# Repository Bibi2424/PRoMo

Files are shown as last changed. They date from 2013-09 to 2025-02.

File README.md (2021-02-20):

# PRoMo

## "Plateforme pour la Robotique Mobile"

### Mobile Robotic Plateform

This project is about creating a mobile robot from scratch.
There are four major parts in this project :

- Mechanics : Build a differential drive plateform with two DC motors with encoders. The different components must be build with Laser cutting and 3D printing (from low cost websites).
			
- Electronics : Create a main board based on a STM32F4 microcontroller with many components like motors, sensors, actuators, RF transmitters...
			
- Firmware : This can go two ways:
	- Provide a sets of high level librairies for controlling a sets of sensors and actuators and example projects, 
	- Give the code as is but with a performant way of interfacing with it (serial communication)

- Documentation : All the informations to understand the project will be there, with some tutorials. At the moment, used to store local datasheets
			
The aim of this projects is to propose some basics to start mobile robotic for the beginners and to simplify things for advanced people.

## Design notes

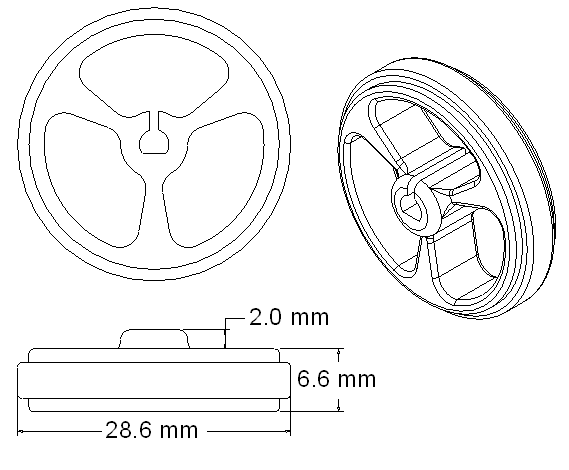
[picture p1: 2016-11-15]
Mechanics/Documentation/Wheel Pololu 32x7.png

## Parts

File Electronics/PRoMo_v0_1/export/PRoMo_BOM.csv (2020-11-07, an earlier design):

Comment | Designator | Footprint | LCSC
100nF | C1,C4,C5,C7,C9,C10,C13,C27,C28,C37,C39 | Capacitor_SMD:C_0805_2012Metric_Pad1.15x1.40mm_HandSolder | C49678
10uF | C11,C32 | Capacitor_SMD:C_0805_2012Metric_Pad1.15x1.40mm_HandSolder | C15850
1uF | C12 | Capacitor_SMD:C_0805_2012Metric_Pad1.15x1.40mm_HandSolder | C28323
4.7uF | C40 | Capacitor_SMD:C_0805_2012Metric_Pad1.15x1.40mm_HandSolder | C1779
18pF | C2,C3 | Capacitor_SMD:C_0805_2012Metric_Pad1.15x1.40mm_HandSolder | C1797
10nF | C26,C30 | Capacitor_SMD:C_0805_2012Metric_Pad1.15x1.40mm_HandSolder | C1710
2.2nF | C29 | Capacitor_SMD:C_0805_2012Metric_Pad1.15x1.40mm_HandSolder | C28260
2.2uF | C6,C8,C31 | Capacitor_SMD:C_0805_2012Metric_Pad1.15x1.40mm_HandSolder | C49217
10uF | C35 | Capacitor_Tantalum_SMD:CP_EIA-3216-18_Kemet-A_Pad1.58x1.35mm_HandSolder | C7171
SS14 | D14 | Diode_SMD:D_SMA_Handsoldering | C2480
LED_Red | D15 | LED_SMD:LED_0805_2012Metric_Pad1.15x1.40mm_HandSolder | C84256
LED_Yellow | D16 | LED_SMD:LED_0805_2012Metric_Pad1.15x1.40mm_HandSolder | C2296
LED_Green | D17,D18 | LED_SMD:LED_0805_2012Metric_Pad1.15x1.40mm_HandSolder | C2297
D_Zener_Small | D19 | Diode_SMD:D_SMA_Handsoldering | C2480
LED_Blue | D1,D2 | LED_SMD:LED_0805_2012Metric_Pad1.15x1.40mm_HandSolder | C2293
Yellow | D20,D21 | LED_SMD:LED_0805_2012Metric_Pad1.15x1.40mm_HandSolder | C2296
22uh | L1 | Inductor_SMD:L_0805_2012Metric_Pad1.15x1.40mm_HandSolder | C32375
10k | R11,R14 | Resistor_SMD:R_0805_2012Metric_Pad1.15x1.40mm_HandSolder | C17414
47R | R12,R13,R24 | Resistor_SMD:R_0805_2012Metric_Pad1.15x1.40mm_HandSolder | C17714
47k | R20 | Resistor_SMD:R_0805_2012Metric_Pad1.15x1.40mm_HandSolder | C17713
470R | R21 | Resistor_SMD:R_0805_2012Metric_Pad1.15x1.40mm_HandSolder | C17710
330R | R22 | Resistor_SMD:R_0805_2012Metric_Pad1.15x1.40mm_HandSolder | C17630
220R | R23,R25,R26 | Resistor_SMD:R_0805_2012Metric_Pad1.15x1.40mm_HandSolder | C17557
STM32F405RGTx | U1 | Package_QFP:LQFP-64_10x10mm_P0.5mm | C15742
FT232RL | U11 | Package_SO:SSOP-28_5.3x10.2mm_P0.65mm | C8690
MPU-6050 | U6 | Sensor_Motion:InvenSense_QFN-24_4x4mm_P0.5mm | C24112
DRV8833PWP | U7 | Package_SO:HTSSOP-16-1EP_4.4x5mm_P0.65mm_EP3.4x5mm_Mask2.46x2.31mm_ThermalVias | C50506
LM2596S-5 | U8 | Package_TO_SOT_SMD:TO-263-5_TabPin3 | C10002
AMS1117-3.3 | U9 | Package_TO_SOT_SMD:SOT-223-3_TabPin2 | C6186
Crystal 25MHz | Y1 | Crystal:Crystal_SMD_3225-4Pin_3.2x2.5mm_HandSoldering | C9006

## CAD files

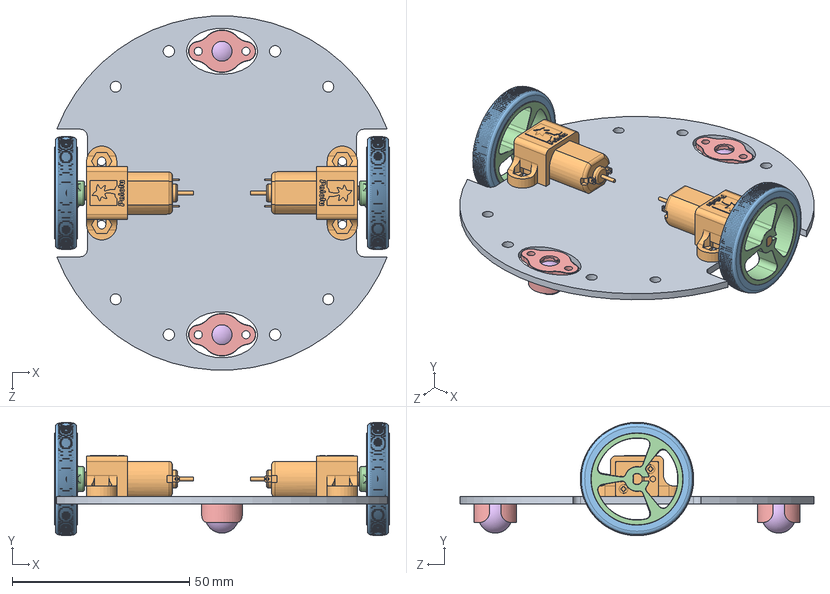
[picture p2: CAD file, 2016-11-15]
Mechanics/PRoMo_v0.1.SLDASM
94.5 x 32.0 x 99.8 mm
Support_bottom
micro-metal-gearmotor-extended-with-1086-bracket x 2
Pololu-Wheel-32x7mm-tire x 2
Pololu-Wheel-32x7mm-rim x 2
Caster x 2
Ball x 2

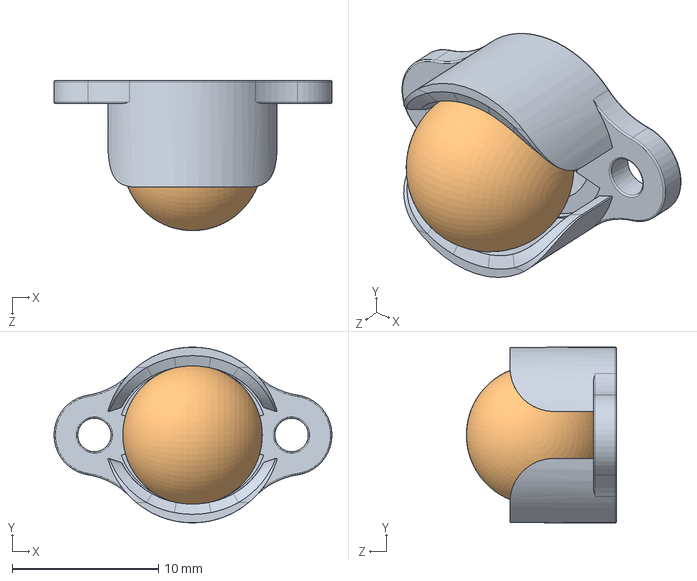
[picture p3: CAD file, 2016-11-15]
Mechanics/Pololu Ball Caster with 3_8_ Metal Ball.SLDASM
19.0 x 12.0 x 10.3 mm
Caster
Ball

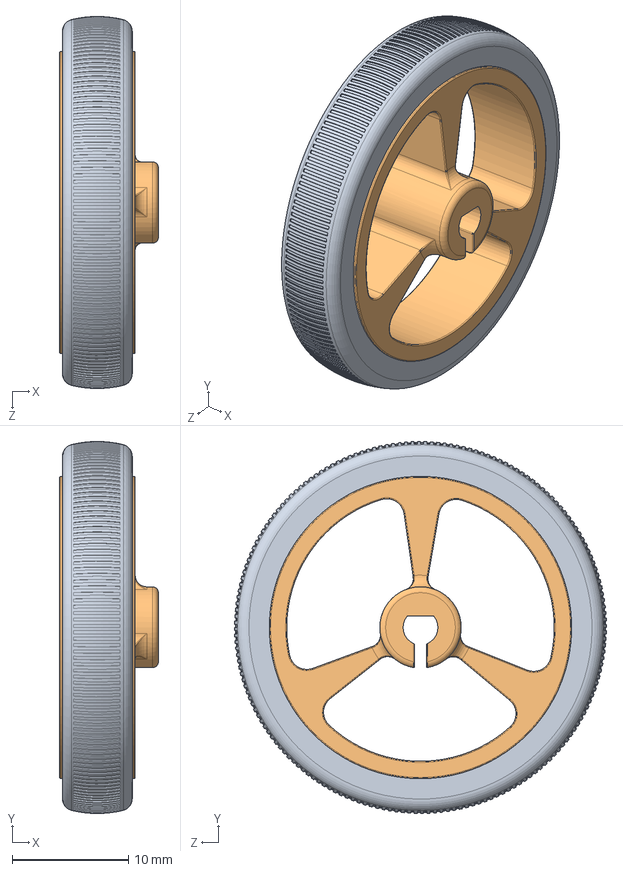
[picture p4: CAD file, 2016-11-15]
Mechanics/Pololu-Wheel-32x7mm.SLDASM
8.50 x 32.0 x 32.0 mm
Pololu-Wheel-32x7mm-tire
Pololu-Wheel-32x7mm-rim

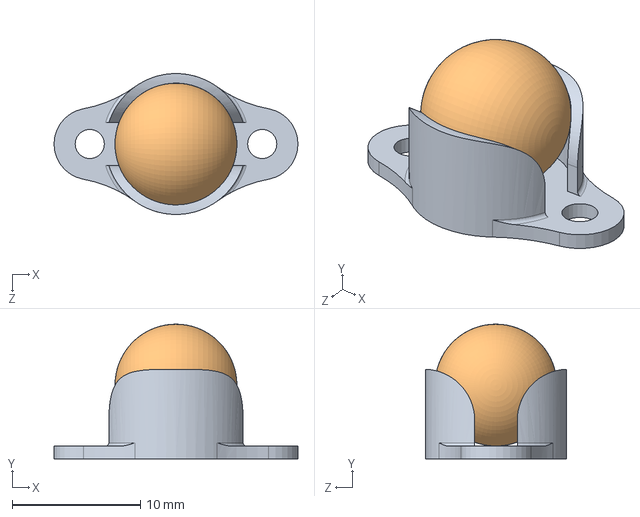
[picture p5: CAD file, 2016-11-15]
Mechanics/Caster ball assembly.SLDASM
19.1 x 10.5 x 11.0 mm
caster ball frame
caster ball

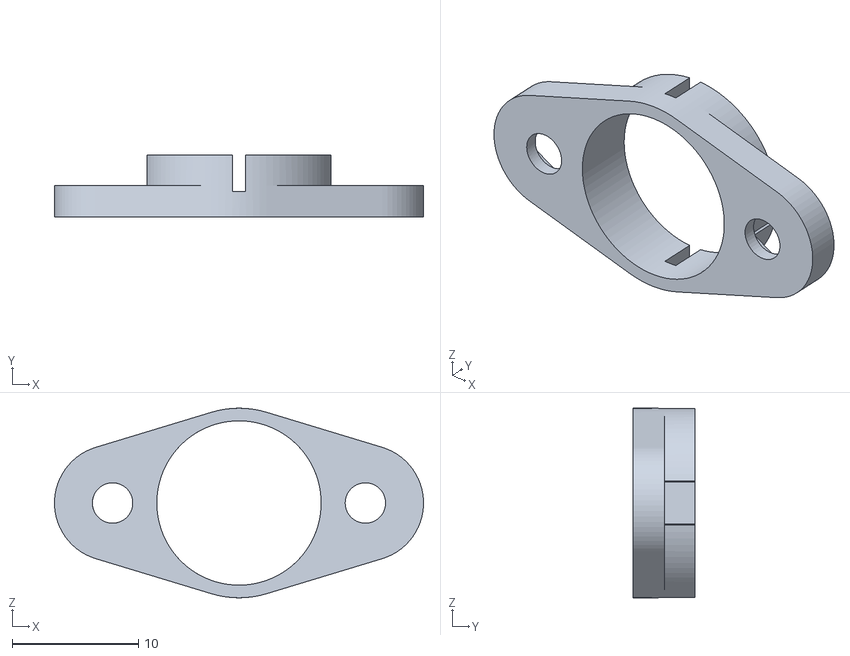
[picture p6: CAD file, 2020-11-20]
Mechanics/BallCaster Support.stl
29.2 x 4.90 x 15.0

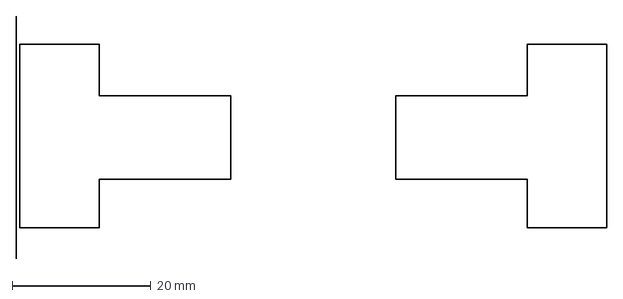
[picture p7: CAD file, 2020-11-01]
Mechanics/Motor_outline.dxf
85.2 x 35.0 mm

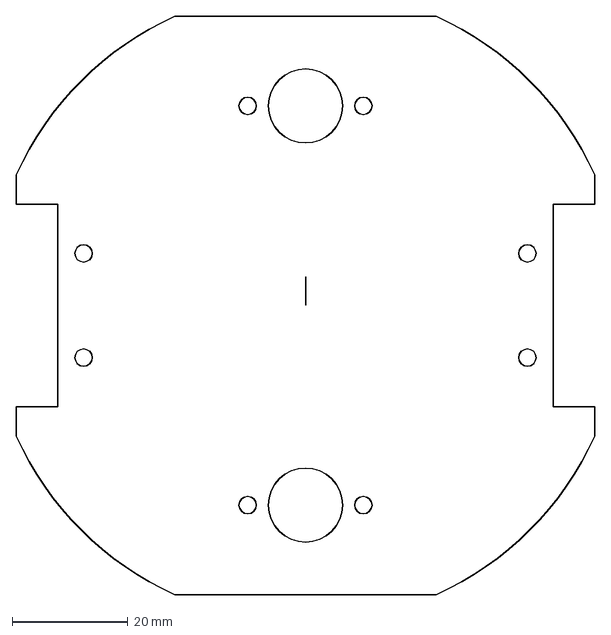
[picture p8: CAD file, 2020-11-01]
Mechanics/Promo_outilne_v2.dxf
100.0 x 100.0 mm

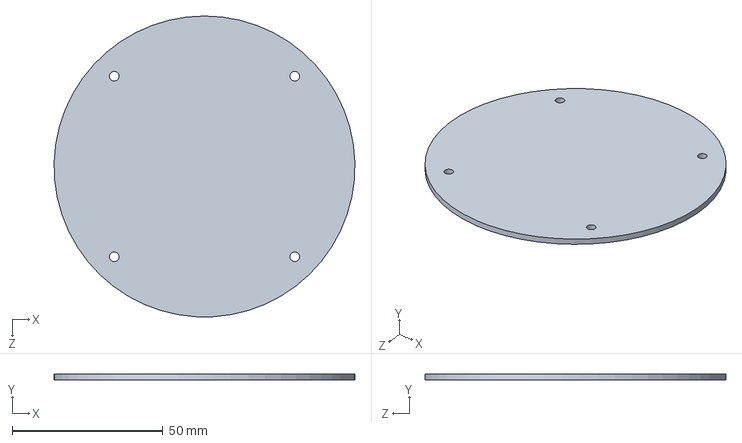
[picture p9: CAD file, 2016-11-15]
Mechanics/Stage1.SLDPRT
100.0 x 2.00 x 100.0 mm

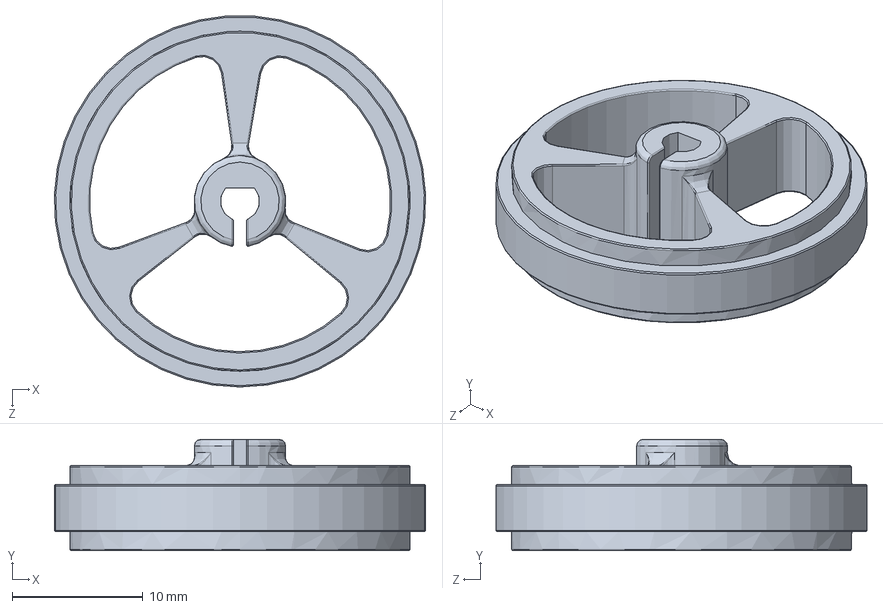
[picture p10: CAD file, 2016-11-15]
Mechanics/Pololu-Wheel-32x7mm-rim.SLDPRT
28.4 x 8.50 x 28.4 mm

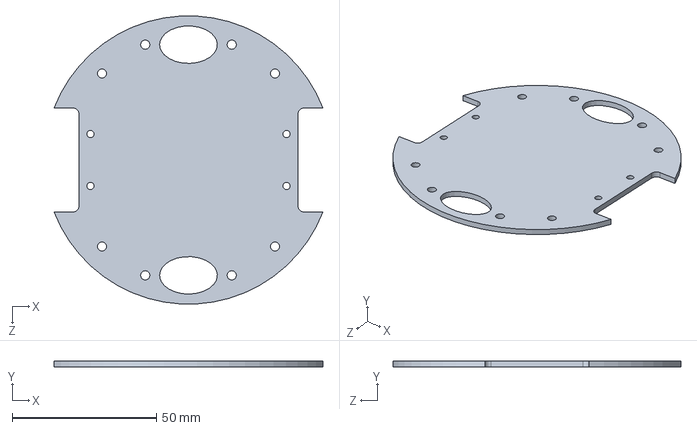
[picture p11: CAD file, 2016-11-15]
Mechanics/Support_bottom.SLDPRT
93.3 x 2.00 x 99.8 mm

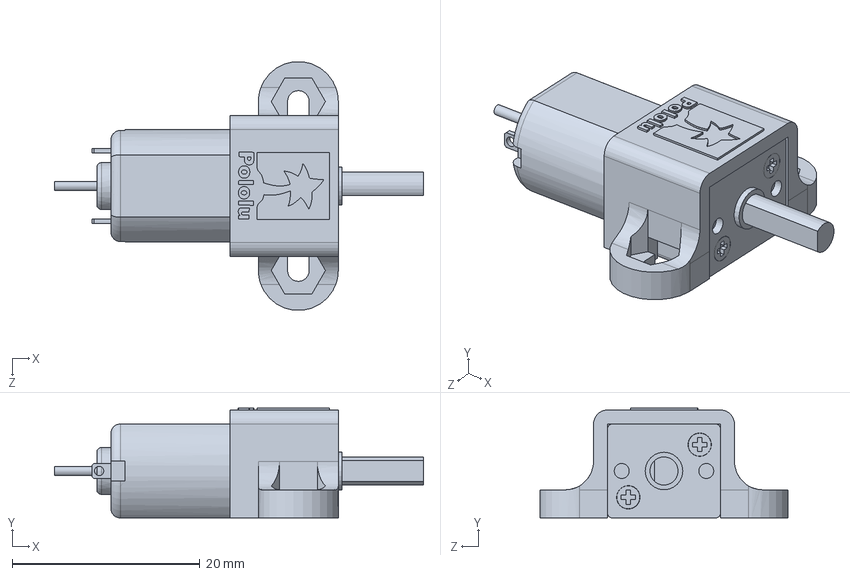
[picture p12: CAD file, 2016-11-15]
Mechanics/micro-metal-gearmotor-extended-with-1086-bracket.SLDPRT
39.3 x 11.7 x 26.4 mm

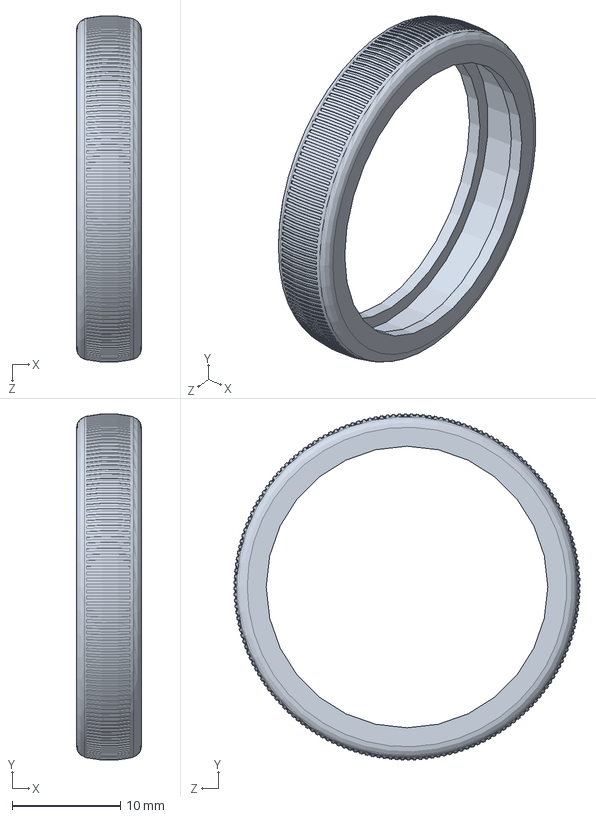
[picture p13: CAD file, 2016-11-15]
Mechanics/Pololu-Wheel-32x7mm-tire.SLDPRT
6.00 x 31.9 x 31.9 mm

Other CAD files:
Mechanics/Ball.sldasm
Mechanics/Caster.sldprt
Mechanics/Ball.sldprt

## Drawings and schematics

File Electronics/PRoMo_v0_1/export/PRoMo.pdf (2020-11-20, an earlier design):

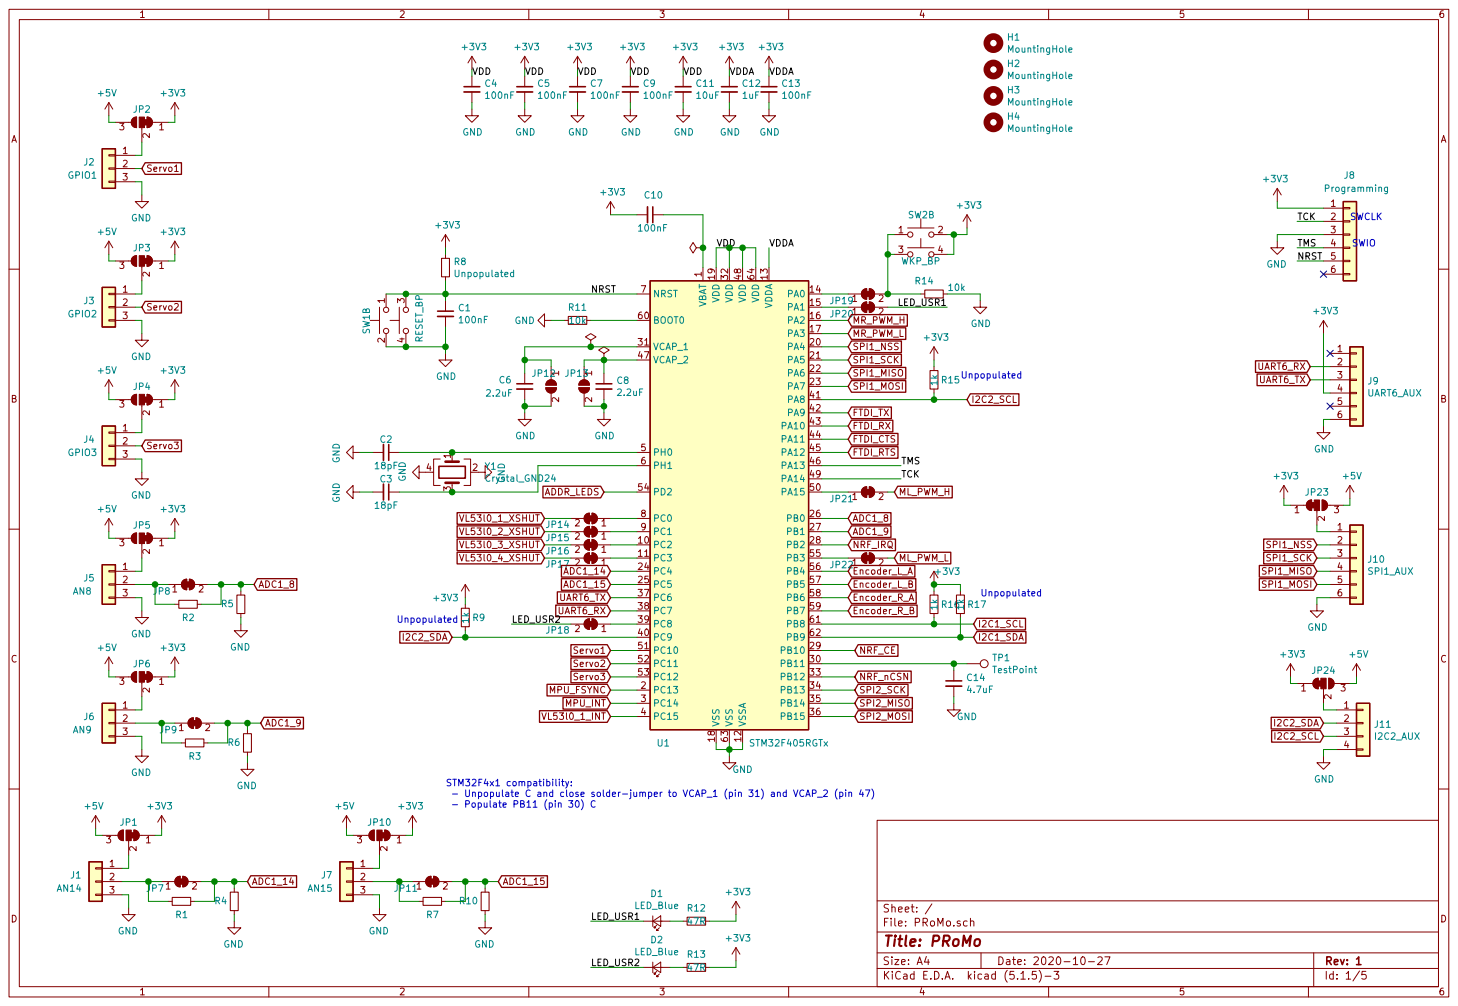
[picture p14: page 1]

1 VCAP_1 31 VCAP_2 47 VDD 19 VDD 32 VDD 48 VDD 64 VDDA 13 VSS 18 VSS 63 VSSA 12 U1 STM32F405RGTx GND GND

STM32F4x1 compatibility:
- Unpopulate C and close solder-jumper to VCAP_1 (pin 31) and VCAP_2 (pin 47)
- Populate PB11 (pin 30) C

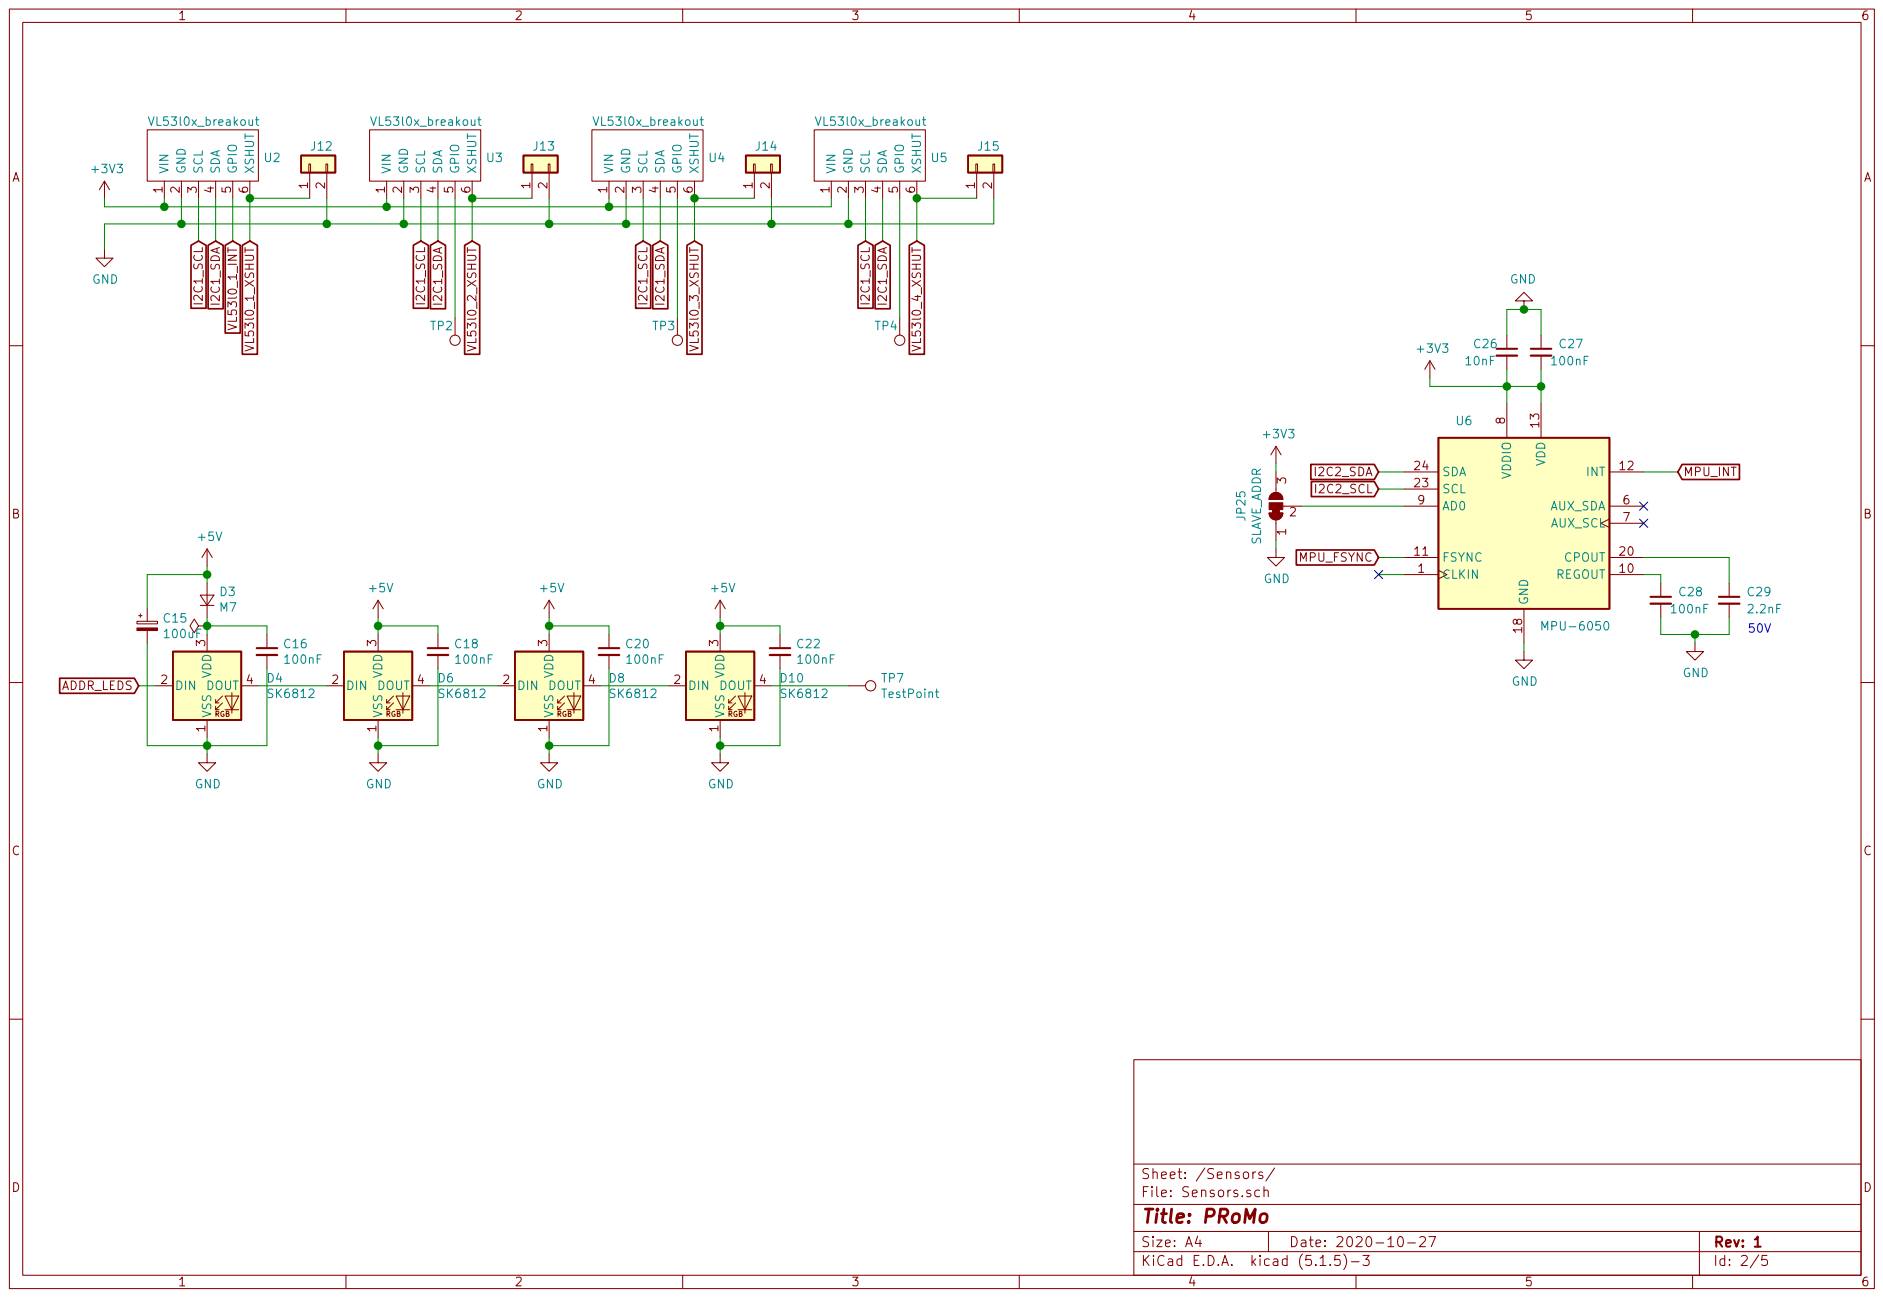
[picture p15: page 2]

6 U4 VL53l0x_breakout VSS RGB 1 DIN 2 VDD
J15 +5V GND

3 DOUT 4 D10 SK6812 TP7 TestPoint TP2 TP3 TP4 VSS RGB 1 DIN 2 VDD

3 JP25 SLAVE_ADDR VSS RGB 1 DIN 2 VDD

3 DOUT 4 D6SK6812 +5V CLKIN 1 REGOUT 10 FSYNC 11

3 DOUT 4 D4SK6812 D3 M7 VSS RGB 1 DIN 2 VDD

File: Sensors.sch Sheet: /Sensors/
Id: 2/5 Title: PRoMo

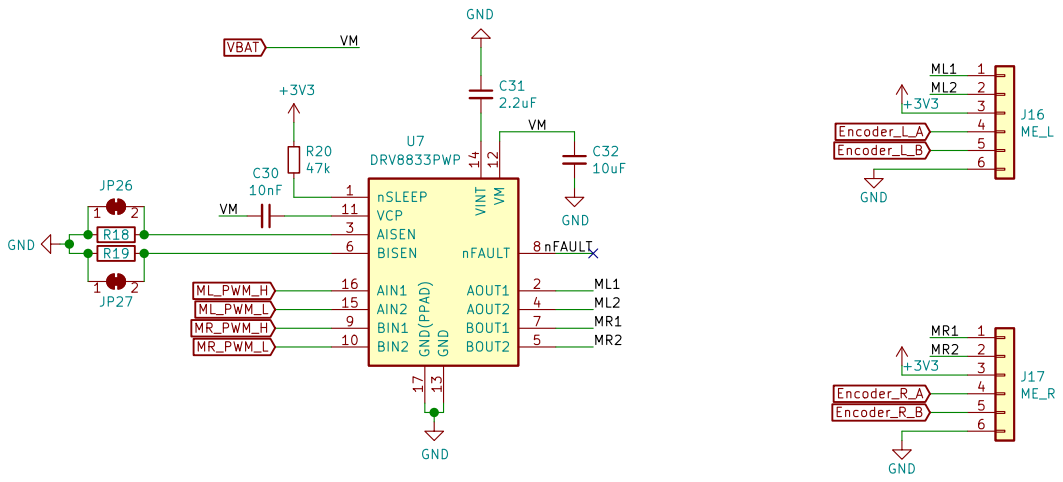
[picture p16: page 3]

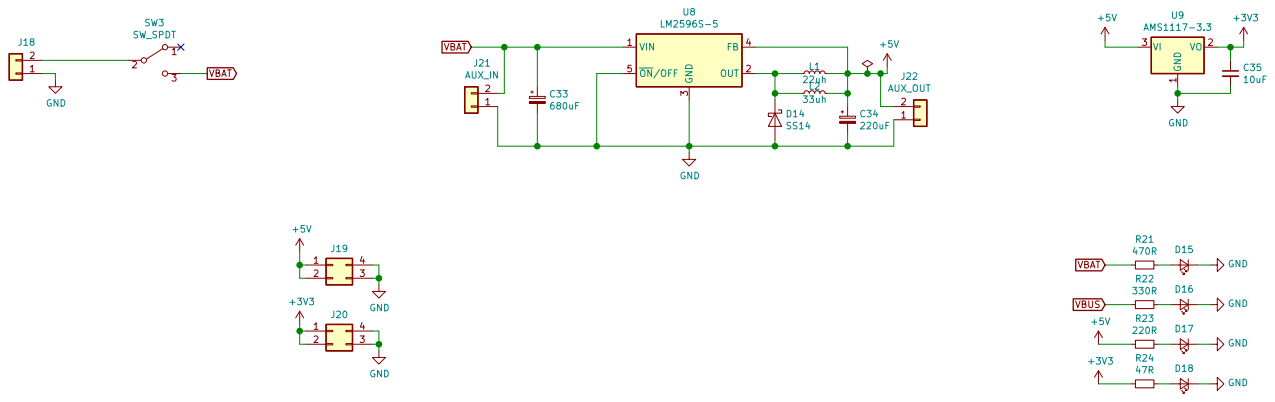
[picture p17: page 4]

File: Power.sch Sheet: /Power/ GND

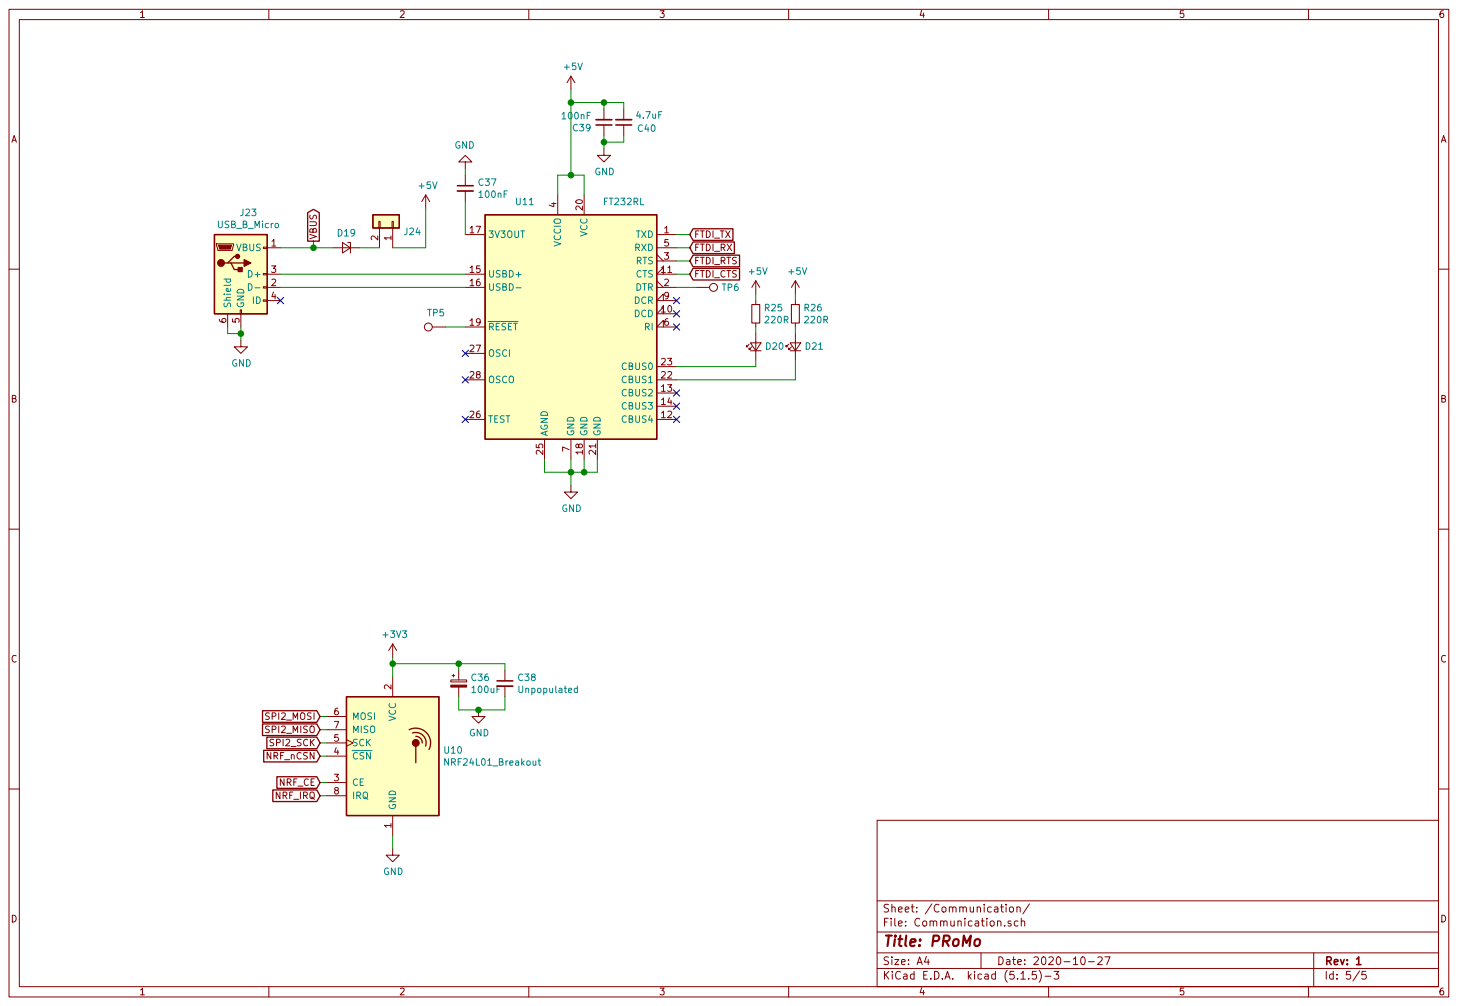
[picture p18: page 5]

2 CE 3 CSN 4 SCK 5 MOSI 6 MISO 7

File: Communication.sch Sheet: /Communication/
Id: 5/5 Title: PRoMo

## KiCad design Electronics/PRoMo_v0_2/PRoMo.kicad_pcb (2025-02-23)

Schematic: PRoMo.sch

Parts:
C1, C2: 18pF; C_0805_2012Metric_Pad1.15x1.40mm_HandSolder; LCSC C1797
C3, C4, C5, C7, C8, C9, C12: 100nF; C_0805_2012Metric_Pad1.15x1.40mm_HandSolder; LCSC C49678
C6: 4.7uF; C_0805_2012Metric_Pad1.15x1.40mm_HandSolder; LCSC C49217
C10: 10uF; C_0805_2012Metric_Pad1.15x1.40mm_HandSolder; LCSC C15850
C11: 1uF; C_0805_2012Metric_Pad1.15x1.40mm_HandSolder; LCSC C28323
D1, D2: LED_Blue; LED_0805_2012Metric_Pad1.15x1.40mm_HandSolder; LCSC C2293
H1, H2, H3, H4: MountingHole; MountingHole_3.2mm_M3
R1, R6, R7, R8: 1k; R_0805_2012Metric_Pad1.15x1.40mm_HandSolder
R2, R3: 10k; R_0805_2012Metric_Pad1.15x1.40mm_HandSolder; LCSC C17714
R4, R5: 47R; R_0805_2012Metric_Pad1.15x1.40mm_HandSolder; LCSC C17714
SW1, SW2, SW3: DIP-BUTTON_2P-6.0X3.0X4.3MM_; SW_PUSH_6mm_H5mm; MPN TS-1101F
U1: STM32F401RETx; LQFP-64_10x10mm_P0.5mm
Y1: Crystal_GND24; Crystal_SMD_3225-4Pin_3.2x2.5mm_HandSoldering; LCSC C9006

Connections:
+3V3: C3.1, C5.1, C7.1, C8.1, C9.2, C10.1, C11.1, C12.1, R1.1, R2.2, R3.2, R4.1, R5.1, R6.1, R7.1, R8.1, U1.13, U1.19, U1.32, U1.48, U1.64; also elsewhere on the board
/AUX_GPIO_1: U1.26
/AUX_GPIO_2: U1.27
/BATT_ADC: U1.25
/BOOT0: U1.60
/BOOT1_BP2: R2.1, SW3.1, U1.28
/BP1: R3.1, SW2.1, U1.2
/LED_USR1: D1.1 (K), U1.55
/LED_USR2: D2.1 (K), U1.43
/SWCLK: U1.49
/SWIO: U1.46
ADC_ML_SENSE: U1.10; also elsewhere on the board
ADC_MR_SENSE: U1.11; also elsewhere on the board
ADDR_LEDS: U1.53; also elsewhere on the board
AUX_SPI_INT: U1.24
AUX_UART_RX: U1.38
AUX_UART_TX: U1.37
DRV_EN: U1.54; also elsewhere on the board
Encoder_L_A: U1.56; also elsewhere on the board
Encoder_L_B: U1.57; also elsewhere on the board
Encoder_R_A: U1.58; also elsewhere on the board
Encoder_R_B: U1.59; also elsewhere on the board
GND: C1.2, C2.2, C3.2, C4.2, C5.2, C6.2, C7.2, C8.2, C10.2, C11.2, C12.2, SW1.1, SW2.2, SW3.2, U1.12, U1.18, U1.31, U1.47, U1.63, Y1.2, Y1.4; also elsewhere on the board
I2C_AUX_INT: U1.39
I2C_AUX_SCL: R6.2, U1.41
I2C_AUX_SDA: R1.2, U1.40
MPU_INT: U1.8; also elsewhere on the board
NRF_CE: U1.29; also elsewhere on the board
NRF_IRQ: U1.9; also elsewhere on the board
NRF_SPI_MISO: U1.35; also elsewhere on the board
NRF_SPI_MOSI: U1.36; also elsewhere on the board
NRF_SPI_SCK: U1.34; also elsewhere on the board
NRF_nCSN: U1.33; also elsewhere on the board
NRST: C4.1, SW1.2, U1.7; also elsewhere on the board
unnamed: C1.1, U1.5, Y1.1
unnamed: C2.1, U1.6, Y1.3
unnamed: C6.1, U1.30
unnamed: C9.1, U1.1
unnamed: D1.2 (A), R4.2
unnamed: D2.2 (A), R5.2
PWM_ML_H: U1.14
PWM_ML_L: U1.15
PWM_MR_H: U1.16
PWM_MR_L: U1.17
SPI_AUX_MISO: U1.22
SPI_AUX_MOSI: U1.23
SPI_AUX_NSS: U1.20
SPI_AUX_SCK: U1.21
USB_DM: U1.44
USB_DP: U1.45
USB_VBUS: U1.42
VL53l0_1_INT: U1.50; also elsewhere on the board
VL53l0_1_XSHUT: U1.51; also elsewhere on the board
VL53l0_2_XSHUT: U1.52; also elsewhere on the board
VL53l0_3_XSHUT: U1.3; also elsewhere on the board
VL53l0_4_XSHUT: U1.4; also elsewhere on the board
VL53l0_I2C_SCL: R7.2, U1.61; also elsewhere on the board
VL53l0_I2C_SDA: R8.2, U1.62; also elsewhere on the board

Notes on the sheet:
TODO: - Remove optimization for JLCPCB PCBA service - Change default MCU for STM32F401 - Change Button footprint - Add diode between power levels - Investigate why VBAT in back driven from 5V/3V3? - Less bright LEDs - Move TIM2 away from PA15 (default state high) - Change programaming connector int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
- 1x 100nF Cap for each VDD pin - 1x 10uF tantalum or ceramic for the chip - 1x 100nF for VBAT - 1x 100nF Ceramic + 1x 1uF tantalum or ceramic for VDDA/VREF
Unpopulated
DONE: - Current sensing from driver chip needs to be connected to ADC pins - Battery monitoring (bridge divider to ADC pin) - PB2 is BOOT1 pin, look into it - change ALEDs pin to PC12 (SPI3 MOSI) - DRV8833 nSLEEP to NRST doesn't work, put it on a GPIO instead - Fix UART TX/RX Inversion on FTDI port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

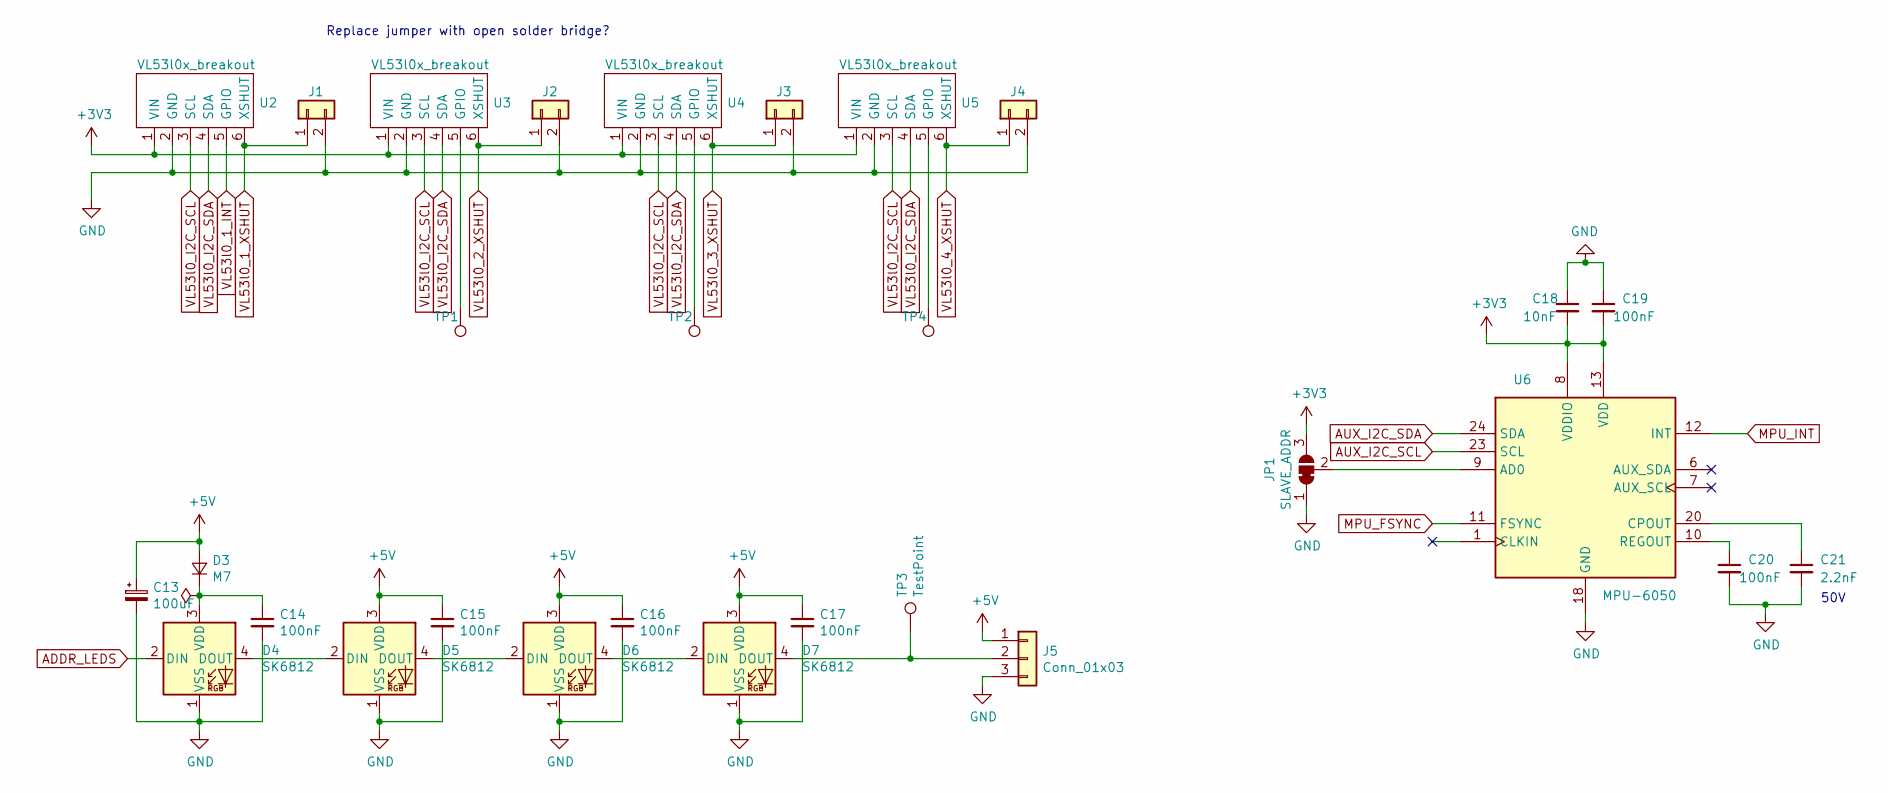
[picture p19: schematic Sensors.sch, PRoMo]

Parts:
C13: 100uF; CP_Radial_D6.3mm_P2.50mm
C14, C15, C16, C17: 100nF; C_0805_2012Metric_Pad1.15x1.40mm_HandSolder
C18: 10nF; C_0805_2012Metric_Pad1.15x1.40mm_HandSolder; LCSC C1710
C19, C20: 100nF; C_0805_2012Metric_Pad1.15x1.40mm_HandSolder; LCSC C49678
C21: 2.2nF; C_0805_2012Metric_Pad1.15x1.40mm_HandSolder; LCSC C28260
D3: M7; D_0805_2012Metric_Pad1.15x1.40mm_HandSolder
D4, D5, D6, D7: SK6812; LED_SK6812_PLCC4_5.0x5.0mm_P3.2mm
J1, J2, J3, J4: Conn_01x02; PinHeader_1x02_P2.54mm_Vertical
J5: Conn_01x03; PinHeader_1x03_P2.54mm_Vertical
JP1: SLAVE_ADDR; SolderJumper-3_P1.3mm_Bridged12_Pad1.0x1.5mm
TP1, TP2, TP3, TP4: TestPoint; TestPoint_Pad_D1.5mm
U2, U3, U4, U5: VL53l0x_breakout; PinSocket_1x06_P2.54mm_Vertical
U6: MPU-6050; InvenSense_QFN-24_4x4mm_P0.5mm; LCSC C24112

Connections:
+3V3: C18.2, C19.2, JP1.3 (B), U2.1 (VIN), U3.1 (VIN), U4.1 (VIN), U5.1 (VIN), U6.8 (VDDIO), U6.13 (VDD); also elsewhere on the board
+5V: C13.1, C15.1, C16.1, C17.1, D3.2 (A), D5.3 (VDD), D6.3 (VDD), D7.3 (VDD), J5.1; also elsewhere on the board
ADDR_LEDS: D4.2 (DIN); also elsewhere on the board
AUX_I2C_SCL: U6.23 (SCL)
AUX_I2C_SDA: U6.24 (SDA)
GND: C13.2, C14.2, C15.2, C16.2, C17.2, C18.1, C19.1, C20.2, C21.2, D4.1 (VSS), D5.1 (VSS), D6.1 (VSS), D7.1 (VSS), J1.2, J2.2, J3.2, J4.2, J5.3, JP1.1 (A), U2.2 (GND), U3.2 (GND), U4.2 (GND), U5.2 (GND), U6.18 (GND); also elsewhere on the board
MPU_FSYNC: U6.11 (FSYNC)
MPU_INT: U6.12 (INT); also elsewhere on the board
unnamed: C14.1, D3.1 (K), D4.3 (VDD)
unnamed: C20.1, U6.10 (REGOUT)
unnamed: C21.1, U6.20 (CPOUT)
unnamed: D4.4 (DOUT), D5.2 (DIN)
unnamed: D5.4 (DOUT), D6.2 (DIN)
unnamed: D6.4 (DOUT), D7.2 (DIN)
unnamed: D7.4 (DOUT), J5.2, TP3.1
unnamed: JP1.2 (C), U6.9 (AD0)
unnamed: TP1.1, U3.5 (GPIO)
unnamed: TP2.1, U4.5 (GPIO)
unnamed: TP4.1, U5.5 (GPIO)
VL53l0_1_INT: U2.5 (GPIO); also elsewhere on the board
VL53l0_1_XSHUT: J1.1, U2.6 (XSHUT); also elsewhere on the board
VL53l0_2_XSHUT: J2.1, U3.6 (XSHUT); also elsewhere on the board
VL53l0_3_XSHUT: J3.1, U4.6 (XSHUT); also elsewhere on the board
VL53l0_4_XSHUT: J4.1, U5.6 (XSHUT); also elsewhere on the board
VL53l0_I2C_SCL: U2.3 (SCL), U3.3 (SCL), U4.3 (SCL), U5.3 (SCL); also elsewhere on the board
VL53l0_I2C_SDA: U2.4 (SDA), U3.4 (SDA), U4.4 (SDA), U5.4 (SDA); also elsewhere on the board

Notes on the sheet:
50V
Replace jumper with open solder bridge?

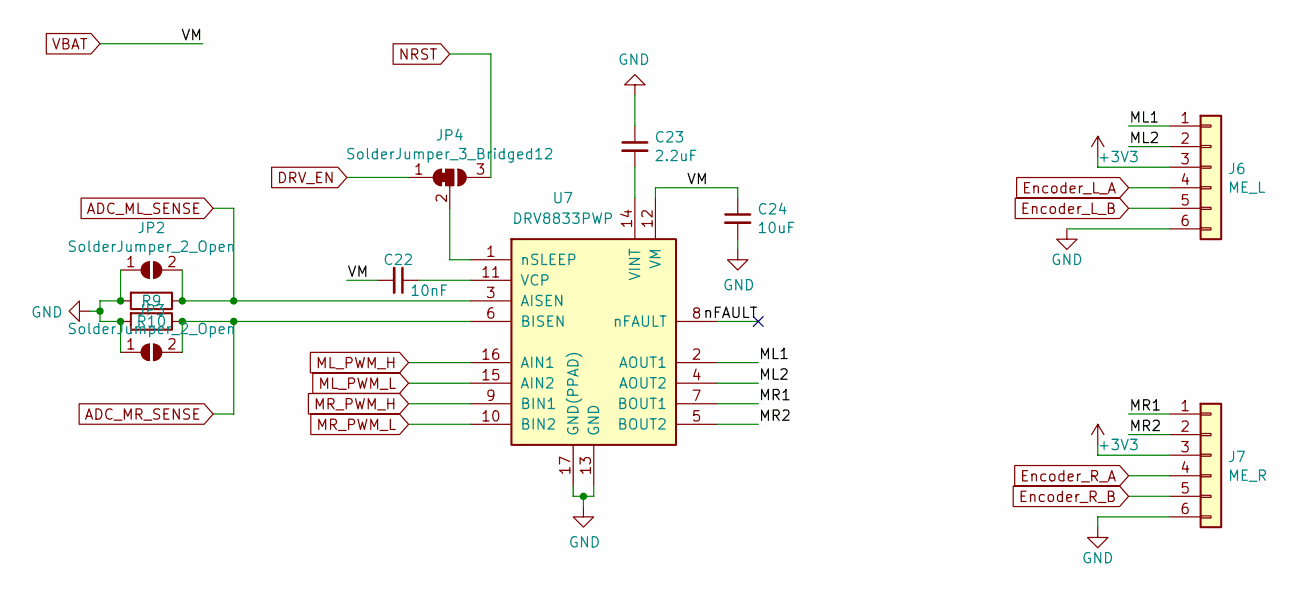
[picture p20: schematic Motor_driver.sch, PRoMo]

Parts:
C22: 10nF; C_0805_2012Metric_Pad1.15x1.40mm_HandSolder; LCSC C1710
C23: 2.2uF; C_0805_2012Metric_Pad1.15x1.40mm_HandSolder; LCSC C49217
C24: 10uF; C_0805_2012Metric_Pad1.15x1.40mm_HandSolder; LCSC C15850
J6: ME_L; PinHeader_1x06_P2.54mm_Vertical
J7: ME_R; PinHeader_1x06_P2.54mm_Vertical
JP2, JP3: SolderJumper_2_Open; SolderJumper-2_P1.3mm_Open_Pad1.0x1.5mm
JP4: SolderJumper_3_Bridged12; SolderJumper-3_P1.3mm_Bridged12_Pad1.0x1.5mm
R9, R10: Sense; R_2512_6332Metric_Pad1.52x3.35mm_HandSolder
U7: DRV8833PWP; HTSSOP-16-1EP_4.4x5mm_P0.65mm_EP3.4x5mm_Mask2.46x2.31mm_The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; LCSC C50506

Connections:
+3V3: J6.3, J7.3; also elsewhere on the board
/Motor_driver/ML1: J6.1, U7.2 (AOUT1)
/Motor_driver/ML2: J6.2, U7.4 (AOUT2)
/Motor_driver/MR1: J7.1, U7.7 (BOUT1)
/Motor_driver/MR2: J7.2, U7.5 (BOUT2)
/Motor_driver/nFAULT: U7.8 (nFAULT)
ADC_ML_SENSE: JP2.2 (B), R9.1, U7.3 (AISEN); also elsewhere on the board
ADC_MR_SENSE: JP3.2 (B), R10.1, U7.6 (BISEN); also elsewhere on the board
DRV_EN: JP4.1 (A); also elsewhere on the board
Encoder_L_A: J6.4; also elsewhere on the board
Encoder_L_B: J6.5; also elsewhere on the board
Encoder_R_A: J7.4; also elsewhere on the board
Encoder_R_B: J7.5; also elsewhere on the board
GND: C23.1, C24.2, J6.6, J7.6, JP2.1 (A), JP3.1 (A), R9.2, R10.2, U7.13 (GND), U7.17 (GND(PPAD)); also elsewhere on the board
ML_PWM_H: U7.16 (AIN1)
ML_PWM_L: U7.15 (AIN2)
MR_PWM_H: U7.9 (BIN1)
MR_PWM_L: U7.10 (BIN2)
NRST: JP4.3 (B); also elsewhere on the board
unnamed: C22.1, U7.11 (VCP)
unnamed: C23.2, U7.14 (VINT)
unnamed: JP4.2 (C), U7.1 (nSLEEP)
VBAT: C22.2, C24.1, U7.12 (VM); also elsewhere on the board

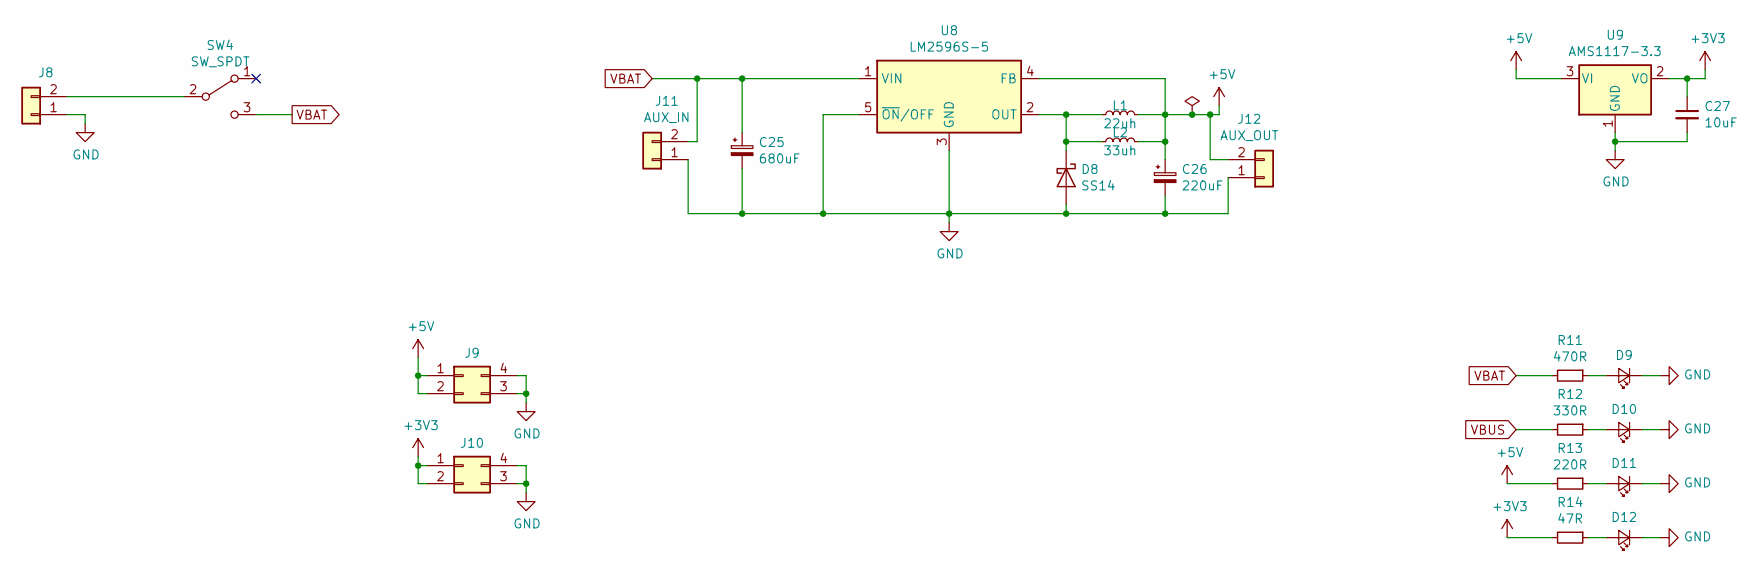
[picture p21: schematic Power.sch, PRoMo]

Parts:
C25: 680uF; CP_Radial_D6.3mm_P2.50mm
C26: 220uF; CP_Radial_D6.3mm_P2.50mm
C27: 10uF; CP_EIA-3216-18_Kemet-A_Pad1.58x1.35mm_HandSolder; LCSC C7171
D8: SS14; D_SMA_Handsoldering; LCSC C2480
D9: LED_Red; LED_0805_2012Metric_Pad1.15x1.40mm_HandSolder; LCSC C84256
D10: LED_Yellow; LED_0805_2012Metric_Pad1.15x1.40mm_HandSolder; LCSC C2296
D11, D12: LED_Green; LED_0805_2012Metric_Pad1.15x1.40mm_HandSolder; LCSC C2297
J8: Conn_01x02; PinHeader_1x02_P2.54mm_Vertical
J9, J10: Conn_02x02_Counter_Clockwise; PinSocket_2x02_P2.54mm_Vertical
J11: AUX_IN; PinHeader_1x02_P2.54mm_Vertical
J12: AUX_OUT; PinHeader_1x02_P2.54mm_Vertical
L1: 22uh; L_0805_2012Metric_Pad1.15x1.40mm_HandSolder; LCSC C32375
L2: 33uh; L_7.3x7.3_H3.5
R11: 470R; R_0805_2012Metric_Pad1.15x1.40mm_HandSolder; LCSC C17710
R12: 330R; R_0805_2012Metric_Pad1.15x1.40mm_HandSolder; LCSC C17630
R13: 220R; R_0805_2012Metric_Pad1.15x1.40mm_HandSolder; LCSC C17557
R14: 47R; R_0805_2012Metric_Pad1.15x1.40mm_HandSolder; LCSC C17714
SW4: SW_SPDT; SW_SPDT_PCM12
U8: LM2596S-5; TO-263-5_TabPin3; LCSC C10002
U9: AMS1117-3.3; SOT-223-3_TabPin2; LCSC C6186

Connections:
+3V3: C27.1, J10.1, J10.2, R14.2, U9.2 (VO); also elsewhere on the board
+5V: C26.1, J9.1, J9.2, J12.2, L1.2, L2.2, R13.2, U8.4 (FB), U9.3 (VI); also elsewhere on the board
GND: C25.2, C26.2, C27.2, D8.2 (A), D9.1 (K), D10.1 (K), D11.1 (K), D12.1 (K), J8.1, J9.3, J9.4, J10.3, J10.4, J11.1, J12.1, U8.3 (GND), U8.5 (~ON~/OFF), U9.1 (GND); also elsewhere on the board
unnamed: D8.1 (K), L1.1, L2.1, U8.2 (OUT)
unnamed: D9.2 (A), R11.1
unnamed: D10.2 (A), R12.1
unnamed: D11.2 (A), R13.1
unnamed: D12.2 (A), R14.1
unnamed: J8.2, SW4.2 (B)
VBAT: C25.1, J11.2, R11.2, SW4.3 (C), U8.1 (VIN); also elsewhere on the board
VBUS: R12.2; also elsewhere on the board

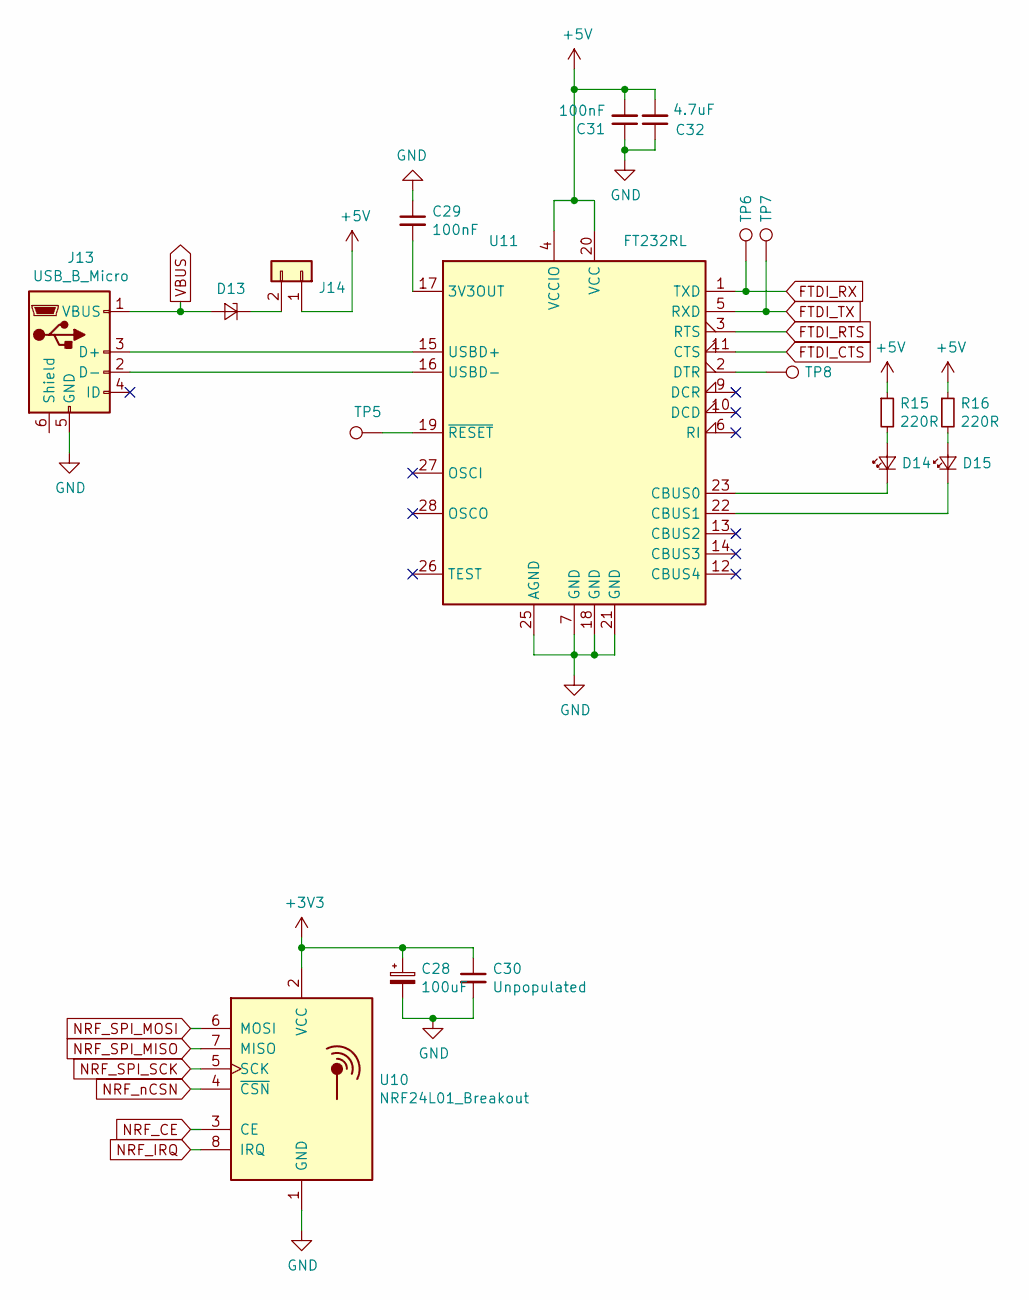
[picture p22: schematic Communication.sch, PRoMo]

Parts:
C28: 100uF; CP_Radial_D6.3mm_P2.50mm
C29, C31: 100nF; C_0805_2012Metric_Pad1.15x1.40mm_HandSolder; LCSC C49678
C30: Unpopulated; C_0805_2012Metric_Pad1.15x1.40mm_HandSolder
C32: 4.7uF; C_0805_2012Metric_Pad1.15x1.40mm_HandSolder; LCSC C1779
D13: D_Zener_Small; D_SMA_Handsoldering; LCSC C2480
D14, D15: Yellow; LED_0805_2012Metric_Pad1.15x1.40mm_HandSolder; LCSC C2296
J13: USB_B_Micro; USB_Micro-B_Molex_47346-0001
J14: Conn_01x02; PinHeader_1x02_P2.54mm_Vertical
R15, R16: 220R; R_0805_2012Metric_Pad1.15x1.40mm_HandSolder; LCSC C17557
TP5, TP6, TP7, TP8: TestPoint; TestPoint_Pad_D1.5mm
U10: NRF24L01_Breakout; nRF24L01_Breakout
U11: FT232RL; SSOP-28_5.3x10.2mm_P0.65mm; LCSC C8690

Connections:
+3V3: C28.1, C30.1, U10.2 (VCC); also elsewhere on the board
+5V: C31.2, C32.2, J14.1, R15.1, R16.1, U11.4 (VCCIO), U11.20 (VCC); also elsewhere on the board
FTDI_RX: TP6.1, U11.1 (TXD)
FTDI_TX: TP7.1, U11.5 (RXD)
GND: C28.2, C29.1, C30.2, C31.1, C32.1, J13.5 (GND), U10.1 (GND), U11.7 (GND), U11.18 (GND), U11.21 (GND), U11.25 (AGND); also elsewhere on the board
NRF_CE: U10.3 (CE); also elsewhere on the board
NRF_IRQ: U10.8 (IRQ); also elsewhere on the board
NRF_SPI_MISO: U10.7 (MISO); also elsewhere on the board
NRF_SPI_MOSI: U10.6 (MOSI); also elsewhere on the board
NRF_SPI_SCK: U10.5 (SCK); also elsewhere on the board
NRF_nCSN: U10.4 (~CSN); also elsewhere on the board
unnamed: C29.2, U11.17 (3V3OUT)
unnamed: D13.1 (K), J14.2
unnamed: D14.1 (K), U11.23 (CBUS0)
unnamed: D14.2 (A), R15.2
unnamed: D15.1 (K), U11.22 (CBUS1)
unnamed: D15.2 (A), R16.2
unnamed: J13.2 (D-), U11.16 (USBD-)
unnamed: J13.3 (D+), U11.15 (USBD+)
unnamed: TP5.1, U11.19 (~RESET~)
unnamed: TP8.1, U11.2 (DTR)
VBUS: D13.2 (A), J13.1 (VBUS); also elsewhere on the board

Board: 2 copper layers, 111 parts (0 on the bottom side), 76 nets, no tracks yet.

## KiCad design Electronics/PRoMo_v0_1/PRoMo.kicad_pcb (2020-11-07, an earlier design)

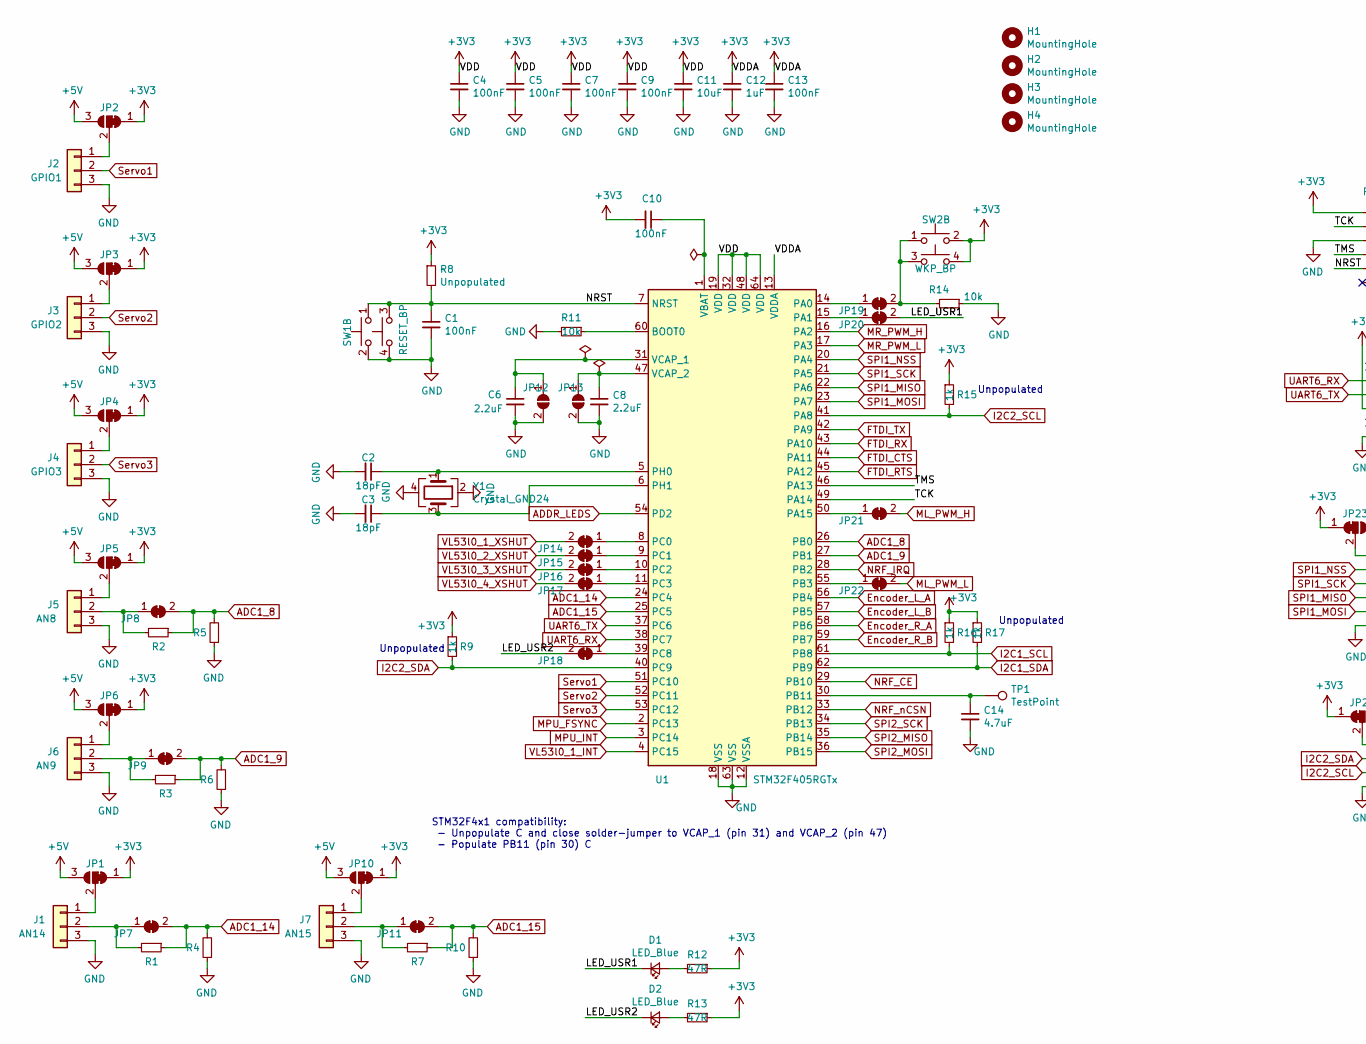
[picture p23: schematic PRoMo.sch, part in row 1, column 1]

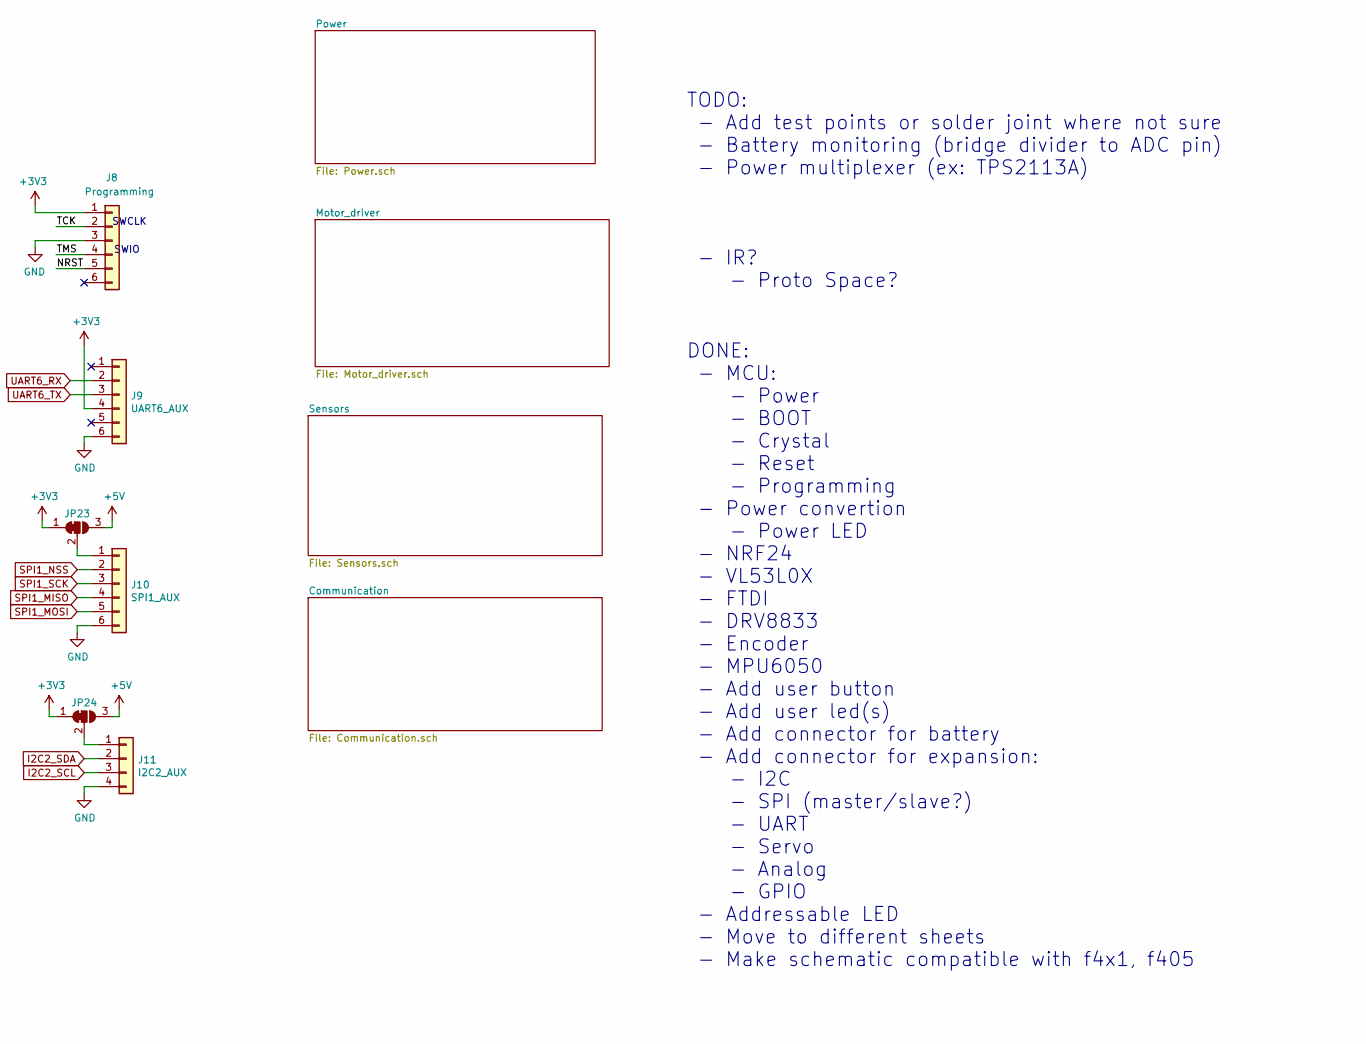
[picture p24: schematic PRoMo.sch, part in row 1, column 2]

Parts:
C1, C4, C5, C7, C9, C10, C13: 100nF; C_0805_2012Metric_Pad1.15x1.40mm_HandSolder; LCSC C49678
C2, C3: 18pF; C_0805_2012Metric_Pad1.15x1.40mm_HandSolder; LCSC C1797
C6, C8: 2.2uF; C_0805_2012Metric_Pad1.15x1.40mm_HandSolder; LCSC C49217
C11: 10uF; C_0805_2012Metric_Pad1.15x1.40mm_HandSolder; LCSC C15850
C12: 1uF; C_0805_2012Metric_Pad1.15x1.40mm_HandSolder; LCSC C28323
C14: 4.7uF; C_0805_2012Metric_Pad1.15x1.40mm_HandSolder
D1, D2: LED_Blue; LED_0805_2012Metric_Pad1.15x1.40mm_HandSolder; LCSC C2293
H1, H2, H3, H4: MountingHole; MountingHole_2.7mm_M2.5
J1: AN14; PinHeader_1x03_P2.54mm_Vertical
J2: GPIO1; PinHeader_1x03_P2.54mm_Vertical
J3: GPIO2; PinHeader_1x03_P2.54mm_Vertical
J4: GPIO3; PinHeader_1x03_P2.54mm_Vertical
J5: AN8; PinHeader_1x03_P2.54mm_Vertical
J6: AN9; PinHeader_1x03_P2.54mm_Vertical
J7: AN15; PinHeader_1x03_P2.54mm_Vertical
J8: Programming; PinHeader_1x06_P2.54mm_Vertical
J9: UART6_AUX; PinHeader_1x06_P2.54mm_Vertical
J10: SPI1_AUX; PinHeader_1x06_P2.54mm_Vertical
J11: I2C2_AUX; PinHeader_1x04_P2.54mm_Vertical
JP1, JP2, JP3, JP4, JP5, JP6, JP10, JP23, JP24: SolderJumper_3_Bridged12; SolderJumper-3_P1.3mm_Bridged12_Pad1.0x1.5mm
JP7, JP8, JP9, JP11, JP14, JP15, JP16, JP17, JP18, JP19, JP20, JP21, JP22: SolderJumper_2_Bridged; SolderJumper-2_P1.3mm_Bridged_Pad1.0x1.5mm
JP12, JP13: SolderJumper_2_Open; SolderJumper-2_P1.3mm_Open_Pad1.0x1.5mm
R1, R2, R3, R4, R5, R6, R7, R9, R10, R15, R16, R17: 1k; R_0805_2012Metric_Pad1.15x1.40mm_HandSolder
R8: Unpopulated; R_0805_2012Metric_Pad1.15x1.40mm_HandSolder
R11, R14: 10k; R_0805_2012Metric_Pad1.15x1.40mm_HandSolder; LCSC C17414
R12, R13: 47R; R_0805_2012Metric_Pad1.15x1.40mm_HandSolder; LCSC C17714
SW1: RESET_BP; SW_TH_Tactile_Omron_B3F-10xx
SW2: WKP_BP; SW_TH_Tactile_Omron_B3F-10xx
TP1: TestPoint; TestPoint_Pad_D1.5mm
U1: STM32F405RGTx; LQFP-64_10x10mm_P0.5mm; LCSC C15742
Y1: Crystal_GND24; Crystal_SMD_3225-4Pin_3.2x2.5mm_HandSoldering; LCSC C9006

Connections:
+3V3: C4.1, C5.1, C7.1, C9.1, C10.2, C11.1, C12.1, C13.1, J8.1, J9.4, JP1.1 (A), JP2.1 (A), JP3.1 (A), JP4.1 (A), JP5.1 (A), JP6.1 (A), JP10.1 (A), JP23.1 (A), JP24.1 (A), R8.1, R9.1, R12.1, R13.1, R15.1, R16.1, R17.1, SW2.2 (D), SW2.4 (D), U1.13 (VDDA), U1.19 (VDD), U1.32 (VDD), U1.48 (VDD), U1.64 (VDD); also elsewhere on the board
+5V: JP1.3 (B), JP2.3 (B), JP3.3 (B), JP4.3 (B), JP5.3 (B), JP6.3 (B), JP10.3 (B), JP23.3 (B), JP24.3 (B); also elsewhere on the board
/LED_USR1: D1.1 (K), JP20.2 (B)
/LED_USR2: D2.1 (K), JP18.2 (B)
/NRST: C1.1, J8.5, R8.2, SW1.1 (C), SW1.3 (C), U1.7 (NRST)
/TCK: J8.2, U1.49 (PA14)
/TMS: J8.4, U1.46 (PA13)
ADC1_8: JP8.2 (B), R2.1, R5.2, U1.26 (PB0)
ADC1_9: JP9.2 (B), R3.1, R6.2, U1.27 (PB1)
ADC1_14: JP7.2 (B), R1.1, R4.2, U1.24 (PC4)
ADC1_15: JP11.2 (B), R7.1, R10.2, U1.25 (PC5)
ADDR_LEDS: U1.54 (PD2); also elsewhere on the board
Encoder_L_A: U1.56 (PB4); also elsewhere on the board
Encoder_L_B: U1.57 (PB5); also elsewhere on the board
Encoder_R_A: U1.58 (PB6); also elsewhere on the board
Encoder_R_B: U1.59 (PB7); also elsewhere on the board
FTDI_CTS: U1.44 (PA11); also elsewhere on the board
FTDI_RTS: U1.45 (PA12); also elsewhere on the board
FTDI_RX: U1.43 (PA10); also elsewhere on the board
FTDI_TX: U1.42 (PA9); also elsewhere on the board
GND: C1.2, C2.2, C3.2, C4.2, C5.2, C6.2, C7.2, C8.2, C9.2, C11.2, C12.2, C13.2, C14.2, J1.3, J2.3, J3.3, J4.3, J5.3, J6.3, J7.3, J8.3, J9.6, J10.6, J11.4, JP12.2 (B), JP13.2 (B), R4.1, R5.1, R6.1, R10.1, R11.2, R14.1, SW1.2 (D), SW1.4 (D), U1.12 (VSSA), U1.18 (VSS), U1.63 (VSS), Y1.2, Y1.4; also elsewhere on the board
I2C1_SCL: R16.2, U1.61 (PB8); also elsewhere on the board
I2C1_SDA: R17.2, U1.62 (PB9); also elsewhere on the board
I2C2_SCL: J11.3, R15.2, U1.41 (PA8); also elsewhere on the board
I2C2_SDA: J11.2, R9.2, U1.40 (PC9); also elsewhere on the board
ML_PWM_H: JP21.2 (B); also elsewhere on the board
ML_PWM_L: JP22.2 (B); also elsewhere on the board
MPU_FSYNC: U1.2 (PC13); also elsewhere on the board
MPU_INT: U1.3 (PC14); also elsewhere on the board
MR_PWM_H: U1.16 (PA2); also elsewhere on the board
MR_PWM_L: U1.17 (PA3); also elsewhere on the board
NRF_CE: U1.29 (PB10); also elsewhere on the board
NRF_IRQ: U1.28 (PB2); also elsewhere on the board
NRF_nCSN: U1.33 (PB12); also elsewhere on the board
unnamed: C2.1, U1.5 (PH0), Y1.1
unnamed: C3.1, U1.6 (PH1), Y1.3
unnamed: C6.1, JP12.1 (A), U1.31 (VCAP_1)
unnamed: C8.1, JP13.1 (A), U1.47 (VCAP_2)
unnamed: C10.1, U1.1 (VBAT)
unnamed: C14.1, TP1.1, U1.30 (PB11)
unnamed: D1.2 (A), R12.2
unnamed: D2.2 (A), R13.2
unnamed: J1.1, JP1.2 (C)
unnamed: J1.2, JP7.1 (A), R1.2
unnamed: J2.1, JP2.2 (C)
unnamed: J3.1, JP3.2 (C)
unnamed: J4.1, JP4.2 (C)
unnamed: J5.1, JP5.2 (C)
unnamed: J5.2, JP8.1 (A), R2.2
unnamed: J6.1, JP6.2 (C)
unnamed: J6.2, JP9.1 (A), R3.2
unnamed: J7.1, JP10.2 (C)
unnamed: J7.2, JP11.1 (A), R7.2
unnamed: J10.1, JP23.2 (C)
unnamed: J11.1, JP24.2 (C)
unnamed: JP14.1 (A), U1.8 (PC0)
unnamed: JP15.1 (A), U1.9 (PC1)
unnamed: JP16.1 (A), U1.10 (PC2)
unnamed: JP17.1 (A), U1.11 (PC3)
unnamed: JP18.1 (A), U1.39 (PC8)
unnamed: JP19.1 (A), U1.14 (PA0)
unnamed: JP19.2 (B), R14.2, SW2.1 (C), SW2.3 (C)
unnamed: JP20.1 (A), U1.15 (PA1)
unnamed: JP21.1 (A), U1.50 (PA15)
unnamed: JP22.1 (A), U1.55 (PB3)
unnamed: R11.1, U1.60 (BOOT0)
SPI1_MISO: J10.4, U1.22 (PA6)
SPI1_MOSI: J10.5, U1.23 (PA7)
SPI1_NSS: J10.2, U1.20 (PA4)
SPI1_SCK: J10.3, U1.21 (PA5)
SPI2_MISO: U1.35 (PB14); also elsewhere on the board
SPI2_MOSI: U1.36 (PB15); also elsewhere on the board
SPI2_SCK: U1.34 (PB13); also elsewhere on the board
Servo1: J2.2, U1.51 (PC10)
Servo2: J3.2, U1.52 (PC11)
Servo3: J4.2, U1.53 (PC12)
UART6_RX: J9.2, U1.38 (PC7)
UART6_TX: J9.3, U1.37 (PC6)
VL53l0_1_INT: U1.4 (PC15); also elsewhere on the board
VL53l0_1_XSHUT: JP14.2 (B); also elsewhere on the board
VL53l0_2_XSHUT: JP15.2 (B); also elsewhere on the board
VL53l0_3_XSHUT: JP16.2 (B); also elsewhere on the board
VL53l0_4_XSHUT: JP17.2 (B); also elsewhere on the board

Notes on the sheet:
SWCLK
SWIO
Unpopulated
DONE: - MCU: - Power - BOOT - Crystal - Reset - Programming - Power convertion - Power LED - NRF24 - VL53L0X - FTDI - DRV8833 - Encoder - MPU6050 - Add user button - Add user led(s) - Add connector for battery - Add connector for expansion: - I2C - SPI (master/slave?) - UART - Servo - Analog - GPIO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
TODO: - Add test points or solder joint where not sure - Battery monitoring (bridge divider to ADC pin) - Power multiplexer (ex: TPS2113A) - IR? - Proto Space?
STM32F4x1 compatibility: - Unpopulate C and close solder-jumper to VCAP_1 (pin 31) and VCAP_2 (pin 47) - Populate PB11 (pin 30) C

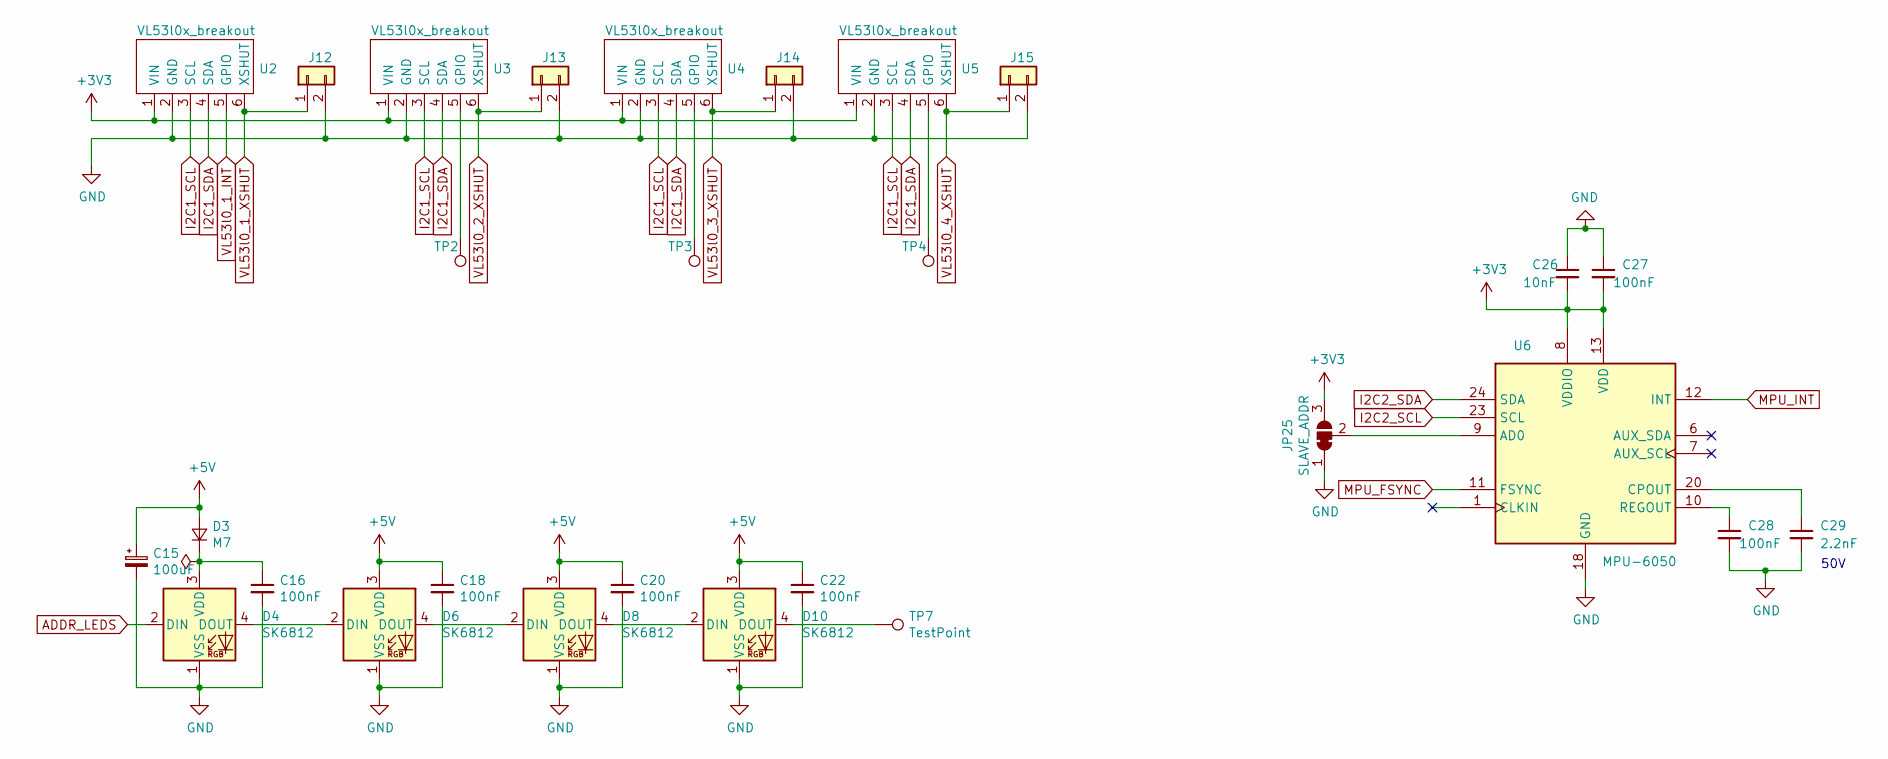
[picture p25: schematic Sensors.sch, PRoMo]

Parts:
C15: 100uF; CP_Radial_D6.3mm_P2.50mm
C16, C18, C20, C22: 100nF; C_0805_2012Metric_Pad1.15x1.40mm_HandSolder
C26: 10nF; C_0805_2012Metric_Pad1.15x1.40mm_HandSolder; LCSC C1710
C27, C28: 100nF; C_0805_2012Metric_Pad1.15x1.40mm_HandSolder; LCSC C49678
C29: 2.2nF; C_0805_2012Metric_Pad1.15x1.40mm_HandSolder; LCSC C28260
D3: M7; D_0805_2012Metric_Pad1.15x1.40mm_HandSolder
D4, D6, D8, D10: SK6812; LED_SK6812_PLCC4_5.0x5.0mm_P3.2mm
J12, J13, J14, J15: Conn_01x02; PinHeader_1x02_P2.54mm_Vertical
JP25: SLAVE_ADDR; SolderJumper-3_P1.3mm_Bridged12_Pad1.0x1.5mm
TP2, TP3, TP4, TP7: TestPoint; TestPoint_Pad_D1.5mm
U2, U3, U4, U5: VL53l0x_breakout; PinSocket_1x06_P2.54mm_Vertical
U6: MPU-6050; InvenSense_QFN-24_4x4mm_P0.5mm; LCSC C24112

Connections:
+3V3: C26.2, C27.2, JP25.3 (B), U2.1 (VIN), U3.1 (VIN), U4.1 (VIN), U5.1 (VIN), U6.8 (VDDIO), U6.13 (VDD); also elsewhere on the board
+5V: C15.1, C18.1, C20.1, C22.1, D3.2 (A), D6.3 (VDD), D8.3 (VDD), D10.3 (VDD); also elsewhere on the board
ADDR_LEDS: D4.2 (DIN); also elsewhere on the board
GND: C15.2, C16.2, C18.2, C20.2, C22.2, C26.1, C27.1, C28.2, C29.2, D4.1 (VSS), D6.1 (VSS), D8.1 (VSS), D10.1 (VSS), J12.2, J13.2, J14.2, J15.2, JP25.1 (A), U2.2 (GND), U3.2 (GND), U4.2 (GND), U5.2 (GND), U6.18 (GND); also elsewhere on the board
I2C1_SCL: U2.3 (SCL), U3.3 (SCL), U4.3 (SCL), U5.3 (SCL); also elsewhere on the board
I2C1_SDA: U2.4 (SDA), U3.4 (SDA), U4.4 (SDA), U5.4 (SDA); also elsewhere on the board
I2C2_SCL: U6.23 (SCL); also elsewhere on the board
I2C2_SDA: U6.24 (SDA); also elsewhere on the board
MPU_FSYNC: U6.11 (FSYNC); also elsewhere on the board
MPU_INT: U6.12 (INT); also elsewhere on the board
unnamed: C16.1, D3.1 (K), D4.3 (VDD)
unnamed: C28.1, U6.10 (REGOUT)
unnamed: C29.1, U6.20 (CPOUT)
unnamed: D4.4 (DOUT), D6.2 (DIN)
unnamed: D6.4 (DOUT), D8.2 (DIN)
unnamed: D8.4 (DOUT), D10.2 (DIN)
unnamed: D10.4 (DOUT), TP7.1
unnamed: JP25.2 (C), U6.9 (AD0)
unnamed: TP2.1, U3.5 (GPIO)
unnamed: TP3.1, U4.5 (GPIO)
unnamed: TP4.1, U5.5 (GPIO)
VL53l0_1_INT: U2.5 (GPIO); also elsewhere on the board
VL53l0_1_XSHUT: J12.1, U2.6 (XSHUT); also elsewhere on the board
VL53l0_2_XSHUT: J13.1, U3.6 (XSHUT); also elsewhere on the board
VL53l0_3_XSHUT: J14.1, U4.6 (XSHUT); also elsewhere on the board
VL53l0_4_XSHUT: J15.1, U5.6 (XSHUT); also elsewhere on the board

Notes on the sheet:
50V

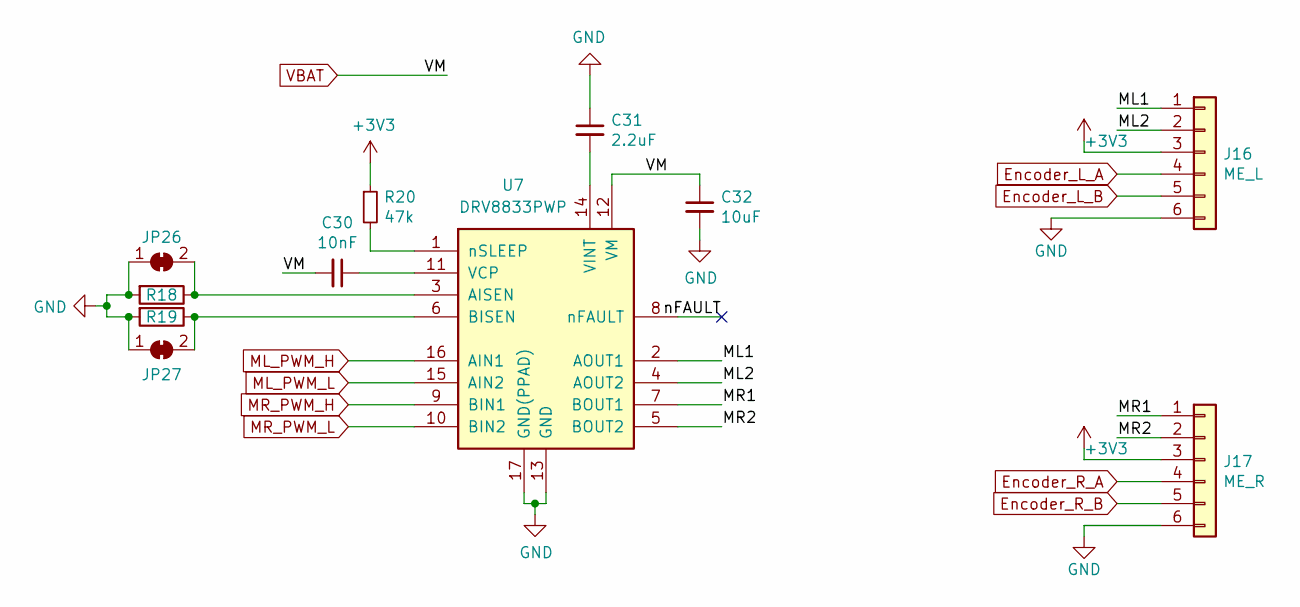
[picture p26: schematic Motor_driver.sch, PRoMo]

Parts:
C30: 10nF; C_0805_2012Metric_Pad1.15x1.40mm_HandSolder; LCSC C1710
C31: 2.2uF; C_0805_2012Metric_Pad1.15x1.40mm_HandSolder; LCSC C49217
C32: 10uF; C_0805_2012Metric_Pad1.15x1.40mm_HandSolder; LCSC C15850
J16: ME_L; PinHeader_1x06_P2.54mm_Vertical
J17: ME_R; PinHeader_1x06_P2.54mm_Vertical
JP26, JP27: SolderJumper_2_Bridged; SolderJumper-2_P1.3mm_Bridged_Pad1.0x1.5mm
R18, R19: Sense; R_2512_6332Metric_Pad1.52x3.35mm_HandSolder
R20: 47k; R_0805_2012Metric_Pad1.15x1.40mm_HandSolder; LCSC C17713
U7: DRV8833PWP; HTSSOP-16-1EP_4.4x5mm_P0.65mm_EP3.4x5mm_Mask2.46x2.31mm_The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; LCSC C50506

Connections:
+3V3: J16.3, J17.3, R20.1; also elsewhere on the board
/Motor_driver/ML1: J16.1, U7.2 (AOUT1)
/Motor_driver/ML2: J16.2, U7.4 (AOUT2)
/Motor_driver/MR1: J17.1, U7.7 (BOUT1)
/Motor_driver/MR2: J17.2, U7.5 (BOUT2)
/Motor_driver/nFAULT: U7.8 (nFAULT)
Encoder_L_A: J16.4; also elsewhere on the board
Encoder_L_B: J16.5; also elsewhere on the board
Encoder_R_A: J17.4; also elsewhere on the board
Encoder_R_B: J17.5; also elsewhere on the board
GND: C31.1, C32.2, J16.6, J17.6, JP26.1 (A), JP27.1 (A), R18.2, R19.2, U7.13 (GND), U7.17 (GND(PPAD)); also elsewhere on the board
ML_PWM_H: U7.16 (AIN1); also elsewhere on the board
ML_PWM_L: U7.15 (AIN2); also elsewhere on the board
MR_PWM_H: U7.9 (BIN1); also elsewhere on the board
MR_PWM_L: U7.10 (BIN2); also elsewhere on the board
unnamed: C30.1, U7.11 (VCP)
unnamed: C31.2, U7.14 (VINT)
unnamed: JP26.2 (B), R18.1, U7.3 (AISEN)
unnamed: JP27.2 (B), R19.1, U7.6 (BISEN)
unnamed: R20.2, U7.1 (nSLEEP)
VBAT: C30.2, C32.1, U7.12 (VM); also elsewhere on the board

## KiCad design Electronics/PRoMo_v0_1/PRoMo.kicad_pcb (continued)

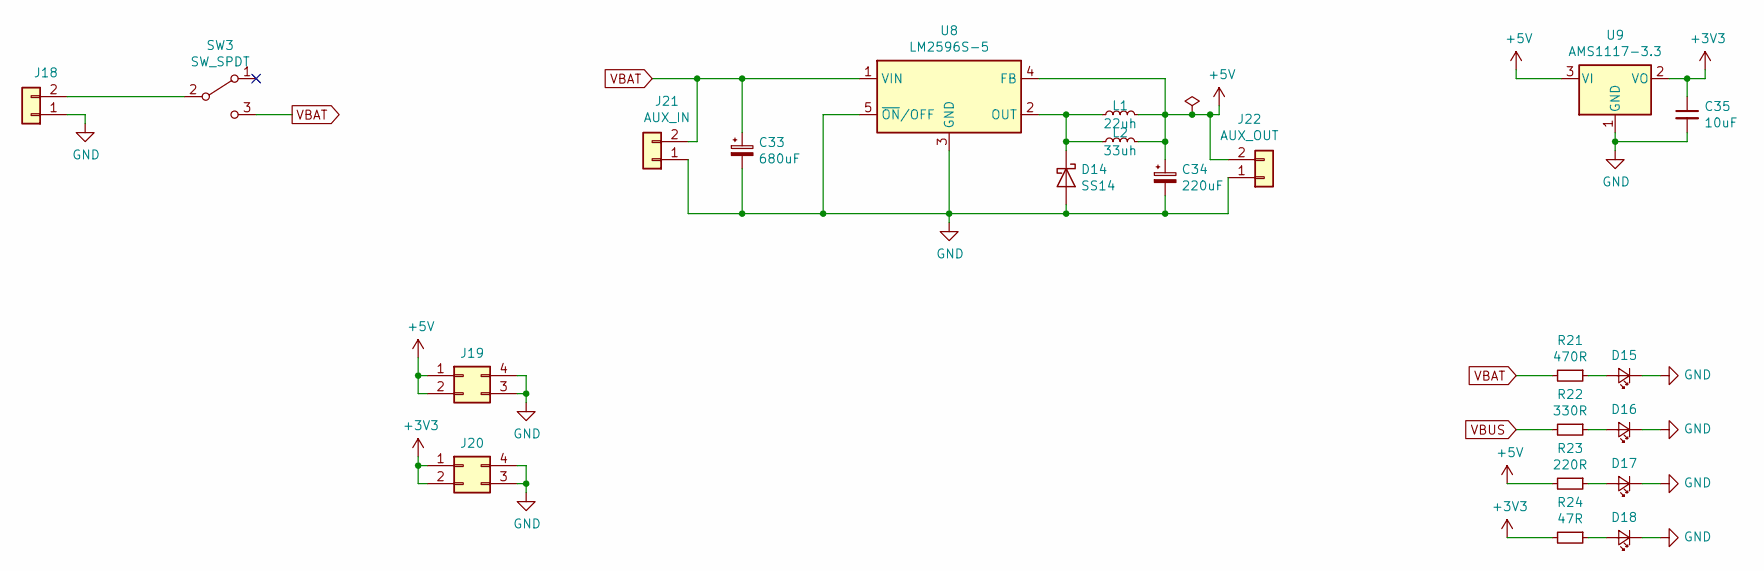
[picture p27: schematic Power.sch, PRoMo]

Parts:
C33: 680uF; CP_Radial_D6.3mm_P2.50mm
C34: 220uF; CP_Radial_D6.3mm_P2.50mm
C35: 10uF; CP_EIA-3216-18_Kemet-A_Pad1.58x1.35mm_HandSolder; LCSC C7171
D14: SS14; D_SMA_Handsoldering; LCSC C2480
D15: LED_Red; LED_0805_2012Metric_Pad1.15x1.40mm_HandSolder; LCSC C84256
D16: LED_Yellow; LED_0805_2012Metric_Pad1.15x1.40mm_HandSolder; LCSC C2296
D17, D18: LED_Green; LED_0805_2012Metric_Pad1.15x1.40mm_HandSolder; LCSC C2297
J18: Conn_01x02; PinHeader_1x02_P2.54mm_Vertical
J19, J20: Conn_02x02_Counter_Clockwise; PinSocket_2x02_P2.54mm_Vertical
J21: AUX_IN; PinHeader_1x02_P2.54mm_Vertical
J22: AUX_OUT; PinHeader_1x02_P2.54mm_Vertical
L1: 22uh; L_0805_2012Metric_Pad1.15x1.40mm_HandSolder; LCSC C32375
L2: 33uh; L_7.3x7.3_H3.5
R21: 470R; R_0805_2012Metric_Pad1.15x1.40mm_HandSolder; LCSC C17710
R22: 330R; R_0805_2012Metric_Pad1.15x1.40mm_HandSolder; LCSC C17630
R23: 220R; R_0805_2012Metric_Pad1.15x1.40mm_HandSolder; LCSC C17557
R24: 47R; R_0805_2012Metric_Pad1.15x1.40mm_HandSolder; LCSC C17714
SW3: SW_SPDT; SW_SPDT_PCM12
U8: LM2596S-5; TO-263-5_TabPin3; LCSC C10002
U9: AMS1117-3.3; SOT-223-3_TabPin2; LCSC C6186

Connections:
+3V3: C35.1, J20.1, J20.2, R24.2, U9.2 (VO); also elsewhere on the board
+5V: C34.1, J19.1, J19.2, J22.2, L1.2, L2.2, R23.2, U8.4 (FB), U9.3 (VI); also elsewhere on the board
GND: C33.2, C34.2, C35.2, D14.2 (A), D15.1 (K), D16.1 (K), D17.1 (K), D18.1 (K), J18.1, J19.3, J19.4, J20.3, J20.4, J21.1, J22.1, U8.3 (GND), U8.5 (~ON~/OFF), U9.1 (GND); also elsewhere on the board
unnamed: D14.1 (K), L1.1, L2.1, U8.2 (OUT)
unnamed: D15.2 (A), R21.1
unnamed: D16.2 (A), R22.1
unnamed: D17.2 (A), R23.1
unnamed: D18.2 (A), R24.1
unnamed: J18.2, SW3.2 (B)
VBAT: C33.1, J21.2, R21.2, SW3.3 (C), U8.1 (VIN); also elsewhere on the board
VBUS: R22.2; also elsewhere on the board

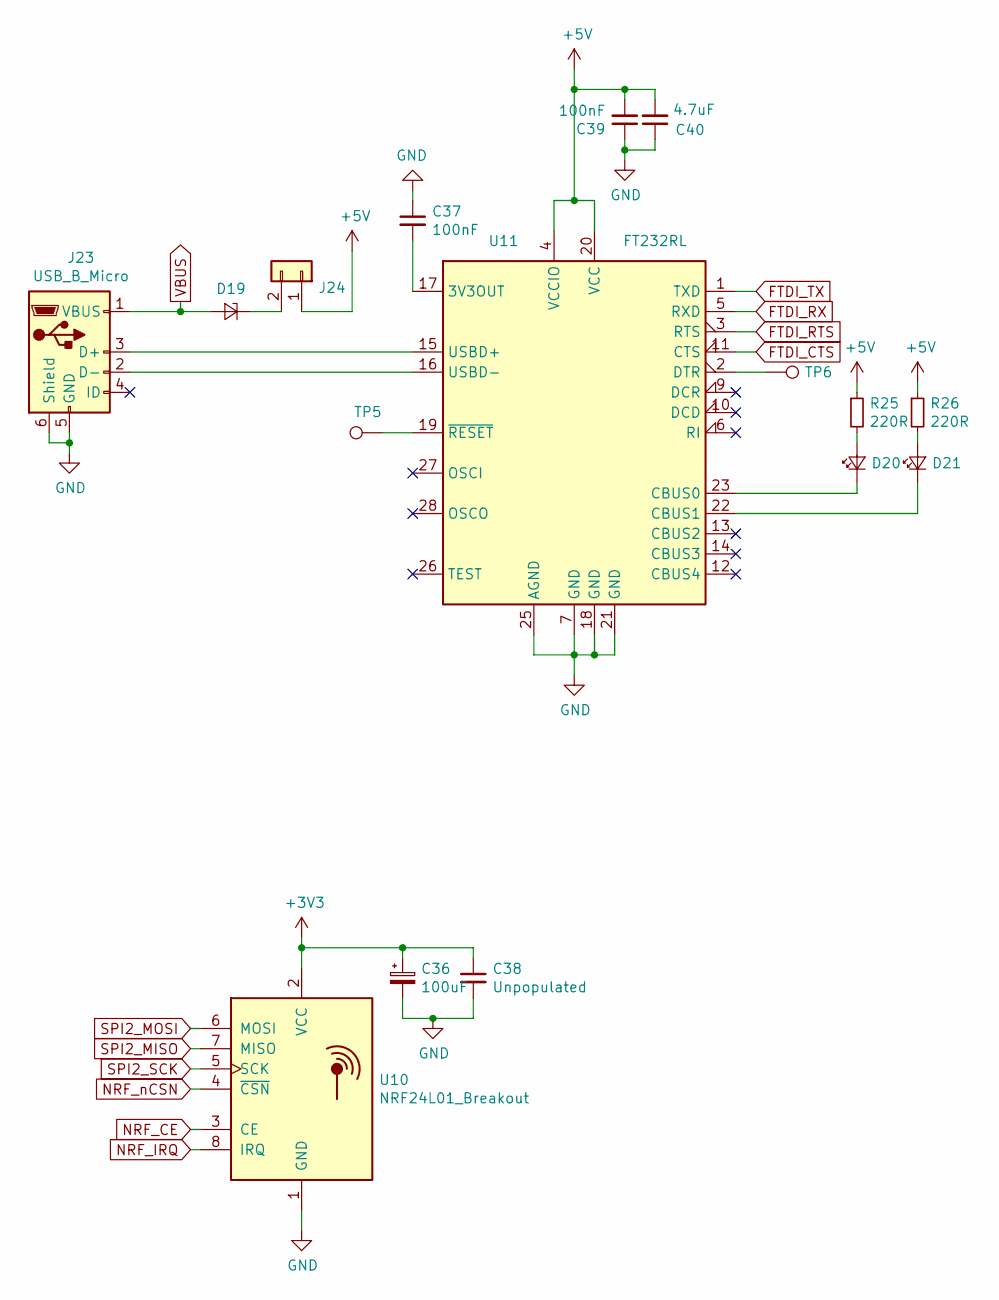
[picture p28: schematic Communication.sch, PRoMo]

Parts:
C36: 100uF; CP_Radial_D6.3mm_P2.50mm
C37, C39: 100nF; C_0805_2012Metric_Pad1.15x1.40mm_HandSolder; LCSC C49678
C38: Unpopulated; C_0805_2012Metric_Pad1.15x1.40mm_HandSolder
C40: 4.7uF; C_0805_2012Metric_Pad1.15x1.40mm_HandSolder; LCSC C1779
D19: D_Zener_Small; D_SMA_Handsoldering; LCSC C2480
D20, D21: Yellow; LED_0805_2012Metric_Pad1.15x1.40mm_HandSolder; LCSC C2296
J23: USB_B_Micro; USB_Micro-B_Molex_47346-0001
J24: Conn_01x02; PinHeader_1x02_P2.54mm_Vertical
R25, R26: 220R; R_0805_2012Metric_Pad1.15x1.40mm_HandSolder; LCSC C17557
TP5, TP6: TestPoint; TestPoint_Pad_D1.5mm
U10: NRF24L01_Breakout; nRF24L01_Breakout
U11: FT232RL; SSOP-28_5.3x10.2mm_P0.65mm; LCSC C8690

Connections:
+3V3: C36.1, C38.1, U10.2 (VCC); also elsewhere on the board
+5V: C39.2, C40.2, J24.1, R25.1, R26.1, U11.4 (VCCIO), U11.20 (VCC); also elsewhere on the board
FTDI_CTS: U11.11 (CTS); also elsewhere on the board
FTDI_RTS: U11.3 (RTS); also elsewhere on the board
FTDI_RX: U11.5 (RXD); also elsewhere on the board
FTDI_TX: U11.1 (TXD); also elsewhere on the board
GND: C36.2, C37.1, C38.2, C39.1, C40.1, J23.5 (GND), J23.6 (Shield), U10.1 (GND), U11.7 (GND), U11.18 (GND), U11.21 (GND), U11.25 (AGND); also elsewhere on the board
NRF_CE: U10.3 (CE); also elsewhere on the board
NRF_IRQ: U10.8 (IRQ); also elsewhere on the board
NRF_nCSN: U10.4 (~CSN); also elsewhere on the board
unnamed: C37.2, U11.17 (3V3OUT)
unnamed: D19.1 (K), J24.2
unnamed: D20.1 (K), U11.23 (CBUS0)
unnamed: D20.2 (A), R25.2
unnamed: D21.1 (K), U11.22 (CBUS1)
unnamed: D21.2 (A), R26.2
unnamed: J23.2 (D-), U11.16 (USBD-)
unnamed: J23.3 (D+), U11.15 (USBD+)
unnamed: TP5.1, U11.19 (~RESET~)
unnamed: TP6.1, U11.2 (DTR)
SPI2_MISO: U10.7 (MISO); also elsewhere on the board
SPI2_MOSI: U10.6 (MOSI); also elsewhere on the board
SPI2_SCK: U10.5 (SCK); also elsewhere on the board
VBUS: D19.2 (A), J23.1 (VBUS); also elsewhere on the board

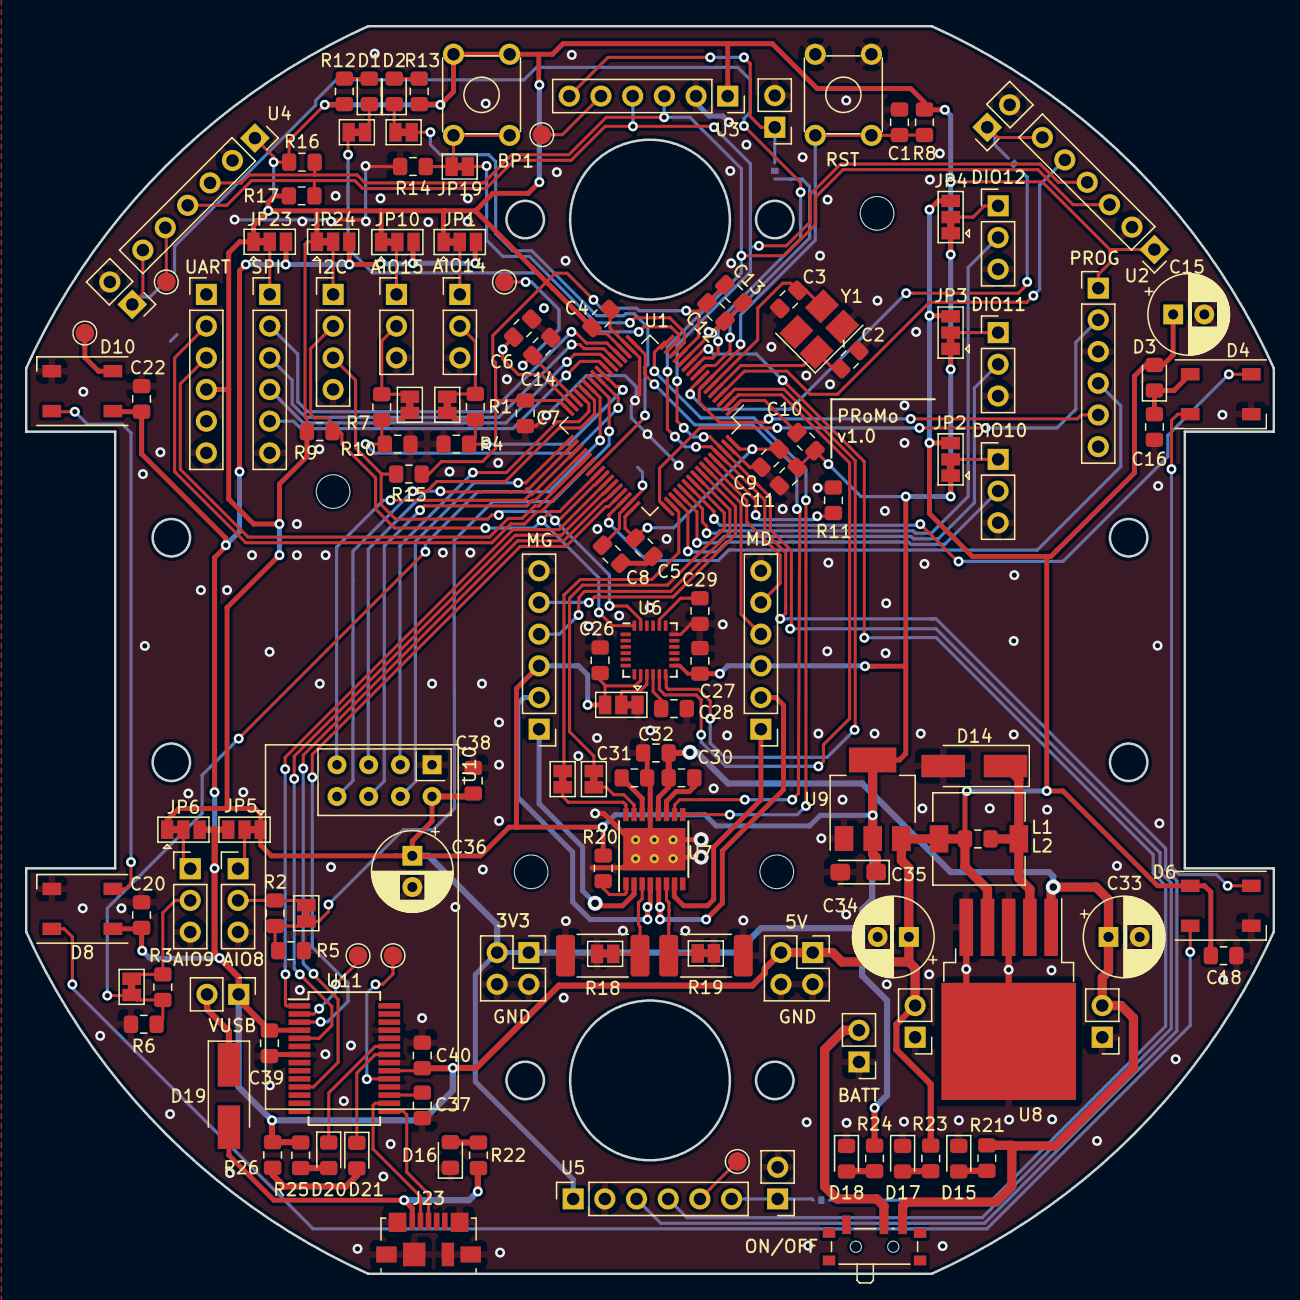
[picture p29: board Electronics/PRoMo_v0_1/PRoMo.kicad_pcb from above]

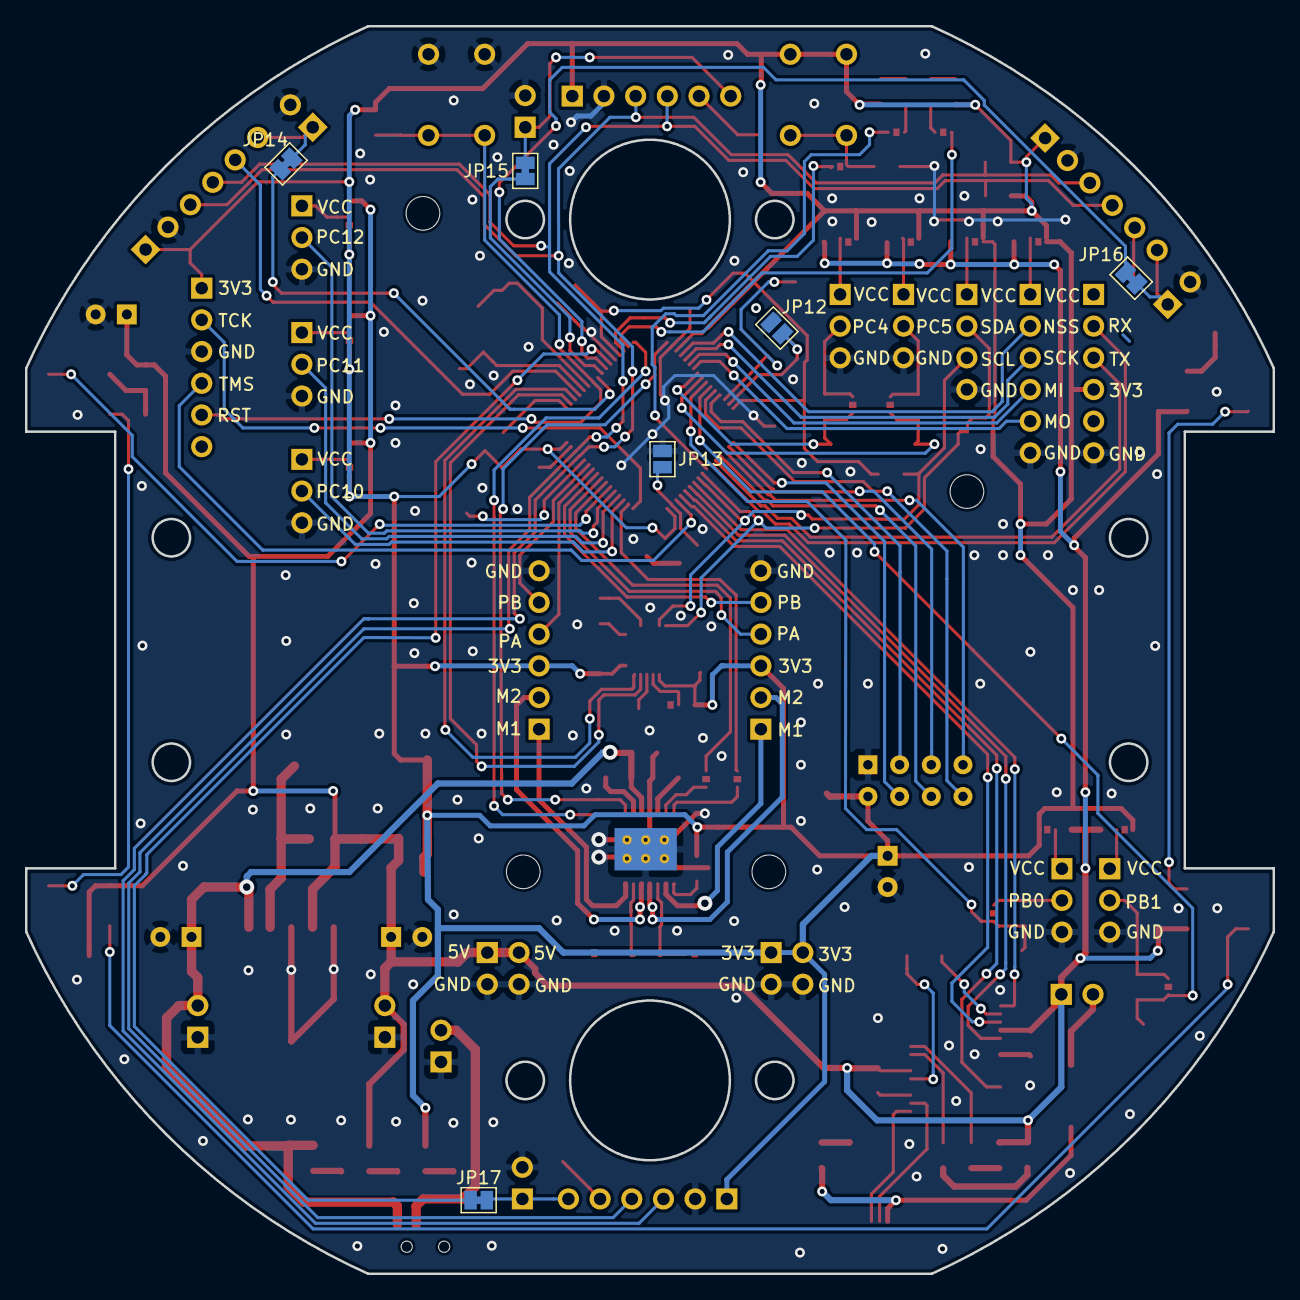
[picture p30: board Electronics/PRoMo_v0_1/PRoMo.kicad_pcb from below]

Board: 2 copper layers, 100.0 x 100.0 mm, 154 parts (6 on the bottom side), 121 nets.

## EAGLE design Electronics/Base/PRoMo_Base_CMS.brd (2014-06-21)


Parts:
BP_RESET: BUTTON-4P-6.2X6.2; 4P-6.2X6.2
BP_USER: BUTTON-4P-6.2X6.2; 4P-6.2X6.2
C1, C10: 100µF; ELECTRO-5.3MM
C2, C3, C4, C6, C8: 100nF; C0805
C7, C11: 10µF; C0805
D1, D2: D'1206'; SOD123
IC1: DSPIC33FJ128MC804-PT; TQFP44
J3: USB-MINIUSB-5P-TH; MINI-5P
JP1, JP2: PINHD-1X22; 1X22
JP3: JP2Q
JP4: PINHD-1X6/90; 1X06/90
JP5: JP3Q
LED3V3, LED5V: LED'1206'; LED-1206
LED_DEBUG1, LED_DEBUG2: LED'1206'; LED-1206
LED_RX1: LED'1206'; LED-1206
LED_TX1: LED'1206'; LED-1206
P1: Bornier; BORNIER_COUDEE_3.5
Q1: MOSFET-P'SI2323CDS/SI2305DS<BR>'; SOT23
R1, R3, R5, R7, R10, R11: 56; R0805
R2, R4, R8: 10k; R0805
R6: 353; R0204/7
R9, R12, R23, R24: R-0805; R0805
REG1: PTH08080W
U1: CJ1117-3.3-1310190P1; SOT223
U2: FT232R-SSOP28; SSOP28

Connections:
!MCLR!: BP_RESET.1 (A0), BP_RESET.4 (A1), IC1.18 (MCLR), JP4.6, R2.1
+3V3: C3.1, C4.1, C6.1, C11.1, IC1.17 (AVDD), IC1.28 (VDD), IC1.40 (VDD1), JP1.3, JP1.4, JP4.5, LED_RX1.+, LED_TX1.+, R2.2, R4.2, R7.1, U1.2 (OUT), U1.TER (OUT), U2.4 (VCCIO)
+5V: C1.+, C2.1, D2.+, JP1.1, JP1.2, Q1.2 (S), R1.1, R8.1, REG1.P$3 (3_VO), U1.3 (IN), U2.20 (VCC)
AN0/RA0: IC1.19 (AN0/VREF+/CN2/RA0), JP3.1, R9.2, R12.2
AN1/RA1: IC1.20 (AN1/VREF-/CN3/RA1), JP3.3, R23.2, R24.2
AN4/RP2/RB2: IC1.23 (AN4/C1IN-/RP2/CN6/RB2), JP2.18
AN5/MISO/RP3/RB3: IC1.24 (AN5/C1IN+/RP3/CN7/RB3), JP2.19
AN6/MOSI/RP16/RC0: IC1.25 (AN6/RP16/CN8/RC0), JP2.20
AN7/CSN/RP17/RC1: IC1.26 (AN7/RP17/CN9/RC1), JP2.21
AN8/SCK/RP18/RC2: IC1.27 (AN8/CVREF/RP18/PMA2/CN10/RC2), JP2.22
BP: BP_USER.1 (A0), BP_USER.4 (A1), JP5.5, R4.1
BP_USER/RA8: IC1.32 (TDO/PMA8/RA8), JP1.20, JP5.6
D+: J3.DP, U2.15 (USBDP)
D-: J3.DM, U2.16 (USBDM)
LED_DEBUG1/RA2: IC1.30 (OSC1/CLKI/CN30/RA2), JP1.22
LED_DEBUG2/RA3: IC1.31 (OSC2/CLKO/CN29/RA3), JP1.21, JP5.4
unnamed: R6.2, REG1.P$4 (4_VOADJ)
unnamed: LED5V.+, R1.2
unnamed: LED_DEBUG1.+, R3.1
unnamed: JP5.1, R3.2
unnamed: LED3V3.+, R7.2
unnamed: C8.2, U2.17 (3V3OUT)
unnamed: R8.2, U2.19 (!RESET)
unnamed: JP2.17, JP3.4, R23.1
unnamed: JP2.16, JP3.2, R9.1
unnamed: R11.1, U2.22 (CBUS1)
unnamed: R5.1, U2.23 (CBUS0)
unnamed: LED_DEBUG2.+, R10.1
unnamed: LED_TX1.-, R5.2
unnamed: JP5.3, R10.2
unnamed: LED_RX1.-, R11.2
PE: BP_RESET.2 (B0), BP_RESET.3 (B1), BP_USER.2 (B0), BP_USER.3 (B1), C1.-, C2.2, C3.2, C4.2, C6.2, C7.2, C8.1, C10.-, C11.2, IC1.6 (VSS), IC1.16 (AVSS), IC1.29 (VSS1), IC1.39 (VSS2), J3.GND, J3.S1 (GND), J3.S2 (GND), J3.S3 (GND), J3.S4 (GND), JP1.5, JP1.6, JP2.3, JP2.4, JP2.5, JP4.4, LED3V3.-, LED5V.-, LED_DEBUG1.-, LED_DEBUG2.-, P1.GND, R6.1, R12.1, R24.1, REG1.P$2 (2_GND), U1.1 (GND), U2.7 (GND), U2.18 (GND), U2.21 (GND), U2.25 (GND), U2.26 (TEST)
PGEC: IC1.22 (PGEC1/AN3/C2IN+/RP1/CN5/RB1), JP4.2
PGED: IC1.21 (PGED1/AN2/C2IN-/RP0/CN4/RB0), JP4.3
PWM1H/RP14/RB14: IC1.14 (PWM1H1/RTCC/RP14/CN12/PMWR/RB14), JP2.14
PWM1L/RP14/RB15: IC1.15 (PWM1L1/RP15/CN11/PMCS1/RB15), JP2.15
PWM2H/RP12/RB12: IC1.10 (PWM1H2/DAC1RP/RP12/CN14/PMD0/RB12), JP2.10
PWM2L/RP13/RB13: IC1.11 (PWM1L2/DAC1RN/RP13/CN13/PMRD/RB13), JP2.11
PWM3H/RP22: IC1.2 (PWM2H1/RP22/CN18/PMA1/RC6), JP1.8
PWM3L/RP23: IC1.3 (PWM2L1/RP23/CN17/PMA0/RC7), JP1.7
QE1A/RP11/RB11: IC1.9 (PGEC2/PWM1L3/RP11/CN15/PMD1/RB11), JP2.9
QE1B/RP10/RB10: IC1.8 (PGED2/PWM1H3/RP10/CN16/PMD2/RB10), JP2.8
QE2A/RP25/RC9: IC1.5 (RP25/CN19/PMA6/RC9), JP2.7
QE2B/RP24/RC8: IC1.4 (RP24/CN20/PMA5/RC8), JP2.6
RA4: IC1.34 (SOSCO/T1CK/CN0/RA4), JP1.18
RA9: IC1.35 (TDI/PMA9/RA9), JP1.17
RP4/RB4: IC1.33 (SOSCI/RP4/CN1/RB4), JP1.19
RP21/RC5: IC1.38 (RP21/CN26/PMA3/RC5), JP1.14
RX_FTDI: IC1.43 (INT0/RP7/CN23/PMD5/RB7), JP1.10, U2.1 (TXD)
SDA/RP5/RB5: IC1.41 (PGED3/ASDA1/RP5/CN27/PMD7/RB5), JP1.13
SDL/RP6/RB6: IC1.42 (PGEC3/ASCL1/RP6/CN24/PMD6/RB6), JP1.12
SENS1/RA7: IC1.13 (TCK/PMA7/RA7), JP2.13
SENS2/RA10: IC1.12 (TMS/PMA10/RA10), JP2.12
SENS3/RP9/RB9: IC1.1 (SDA1/RP9/CN21/PMD3/RB9), JP1.9
TX_FTDI: IC1.44 (SCL1/RP8/CN22/PMD4/RB8), JP1.11, U2.5 (RXD)
UART_AX12/RP19/RC3: IC1.36 (RP19/CN28/PMBE/RC3), JP1.16
UART_BIS/RP20/RC4: IC1.37 (RP20/CN25/PMA4/RC4), JP1.15
V+: D1.+, P1.VCC
VCAP: C7.1, IC1.7 (VCAP/VDDCORE)
VIN: C10.+, D1.-, D2.-, JP2.1, JP2.2, Q1.1 (G), REG1.P$1 (1_VI)
VUSB: J3.VCC, Q1.3 (D)

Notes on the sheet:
Version CMS
TO DO : -> Mettre les empreintes (Jumpers) pour les ponts diviseurs (ANs) -> Faire la BOM
Capas de découplage : A mettre au plus près du PIC


Board: 4 copper layers, 48.0 x 98.0 mm, 45 parts (0 on the bottom side), 61 nets.

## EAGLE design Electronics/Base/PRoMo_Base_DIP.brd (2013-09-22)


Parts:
C1: 100nF; C102-043X133
C2, C5: 100nF; C050-035X075
C3, C7: 10µF; C050-035X075
C4, C6: 100µF; C050-035X075
D1, D2: 1N4004; DO41-10
IC1: DSPIC33FJ64MC802-SP; DIL28-3
J1: JACK-PLUG1; SPC4078
JP1: PINHD-1X6/90; 1X06/90
JP2, JP4: PINHD-1X6; 1X06
JP3, JP9: PINHD-1X9; 1X09
JP10: PINHD-1X4; 1X04
JP12, JP13: JP1E; JP1
LED1, LED2, LED3, LED4: LED3MM
P1: Vin; BORNIER_COUDEE_3.5
P2: 5V; BORNIER_COUDEE_3.5
R1: 10k; 0204/7
REG1: PTH08000W(EUS); TRHOUGH_HOLE_(EUS)
REG_3V3: LM2937TO-220; TO220V
RLED1, RLED2, RLED3, RLED4: 330; 0204/7
RSET: 353; 0204/7
S1: RACON12

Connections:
5V: C5.1, C6.1, D2.C, JP3.1, JP3.2, JP3.3, REG1.6, REG_3V3.1 (VI), RLED4.1
+3V3: C1.1, C2.1, C7.1, IC1.13 (VDD), IC1.28 (AVDD), JP1.2, JP3.4, JP3.5, JP3.6, R1.2, REG_3V3.3 (VO), RLED3.1
AN0: IC1.2 (AN0/VREF+/CN2/RA0), JP2.1
AN1: IC1.3 (AN1/VREF-/CN3/RA1), JP2.2
AN2: IC1.4 (PGD1/AN2/C2IN-/RP0/CN4/RB0), JP2.3
AN3: IC1.5 (PGC1/AN3/C2IN+/RP1/CN5/RB1), JP2.4
AN4: IC1.6 (AN4/C1IN-/RP2/CN6/RB2), JP2.5
AN5: IC1.7 (AN5/C1IN+/RP3/CN7/RB3), JP2.6
MCLR: IC1.1 (!MCLR), JP1.1, R1.1, S1.1 (S)
unnamed: IC1.26 (PWM1L1/RP15/CN11/PMCS1/RB15), JP9.1
unnamed: IC1.25 (PWM1H1/RTCC/RP14/CN12/PMWR/RB14), JP9.2
unnamed: IC1.24 (PWM1L2/RP13/CN13/PMRD/RB13), JP9.3
unnamed: IC1.23 (PWM1H2/RP12/CN14/PMD0/RB12), JP9.4
unnamed: IC1.22 (PGC2/TMS/PWM1L3/RP11/CN15/PMD1/RB11), JP9.5
unnamed: IC1.21 (PGD2/TDI/PWM1H3/RP10/CN16/PMD2/RB10), JP9.6
unnamed: IC1.18 (TDO/PWM2L1/SDA1/RP9/CN21/PMD3/RB9), JP9.7
unnamed: IC1.17 (TCK/PWM2H1/SCL1/RP8/CN22/PMD4/RB8), JP9.8
unnamed: IC1.16 (INT0/RP7/CN23/PMD5/RB7), JP9.9
unnamed: IC1.9 (OSC1/CLKI/CN30/RA2), JP10.1
unnamed: IC1.10 (OSC2/CLKO/CN29/PMA0/RA3), JP10.2
unnamed: LED2.A, RLED2.2
unnamed: LED1.A, RLED1.2
unnamed: LED3.A, RLED3.2
unnamed: JP12.2, RLED1.1
unnamed: JP13.2, RLED2.1
unnamed: D2.A, P2.VCC
unnamed: REG1.5, RSET.2
unnamed: LED4.A, RLED4.2
NC: JP1.6
PE: C1.2, C2.2, C3.2, C4.2, C5.2, C6.2, C7.2, IC1.8 (VSS), IC1.19 (VSS2), IC1.27 (AVSS), J1.1, J1.2, JP1.3, JP3.7, JP3.8, JP3.9, JP4.4, JP4.5, JP4.6, LED1.K (C), LED2.K (C), LED3.K (C), LED4.K (C), P1.GND, P2.GND, REG1.1, REG_3V3.2 (GND), RSET.1, S1.3
PGC: IC1.15 (PGC3/ASCL1/RP6/CN24/PMD6/RB6), JP1.5
PGD: IC1.14 (PGED3/ASDA1/RP5/CN27/PMD7/RB5), JP1.4
RA4: IC1.12 (SOSCO/T1CK/CN0/PMA1/RA4), JP10.4, JP13.1
RB4: IC1.11 (SOSCI/RP4/CN1/PMBE/RB4), JP10.3, JP12.1
VCAP: C3.1, IC1.20 (VCAP/VDDCORE)
VIN: D1.A, J1.3, P1.VCC
VIN_P: C4.1, D1.C, JP4.1, JP4.2, JP4.3, REG1.3

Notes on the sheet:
PicKit3 Connecteur
Capas de découplage : A mettre au plus près du PIC
Gestion du reset
Version Traversante
Vérifier le boitier
Ca va être chaud en traversant
Connecteur Jack 2.5mm pour Vin
Régulateur 5V
Régulateur 3V3
Tulipe Analogique
Tulipe Numérque 1
Tulipe Numérque 2
Tulipe Alimentation 2
LEDs de debug
Vin : 6.1V to 14V
Bornier Vin
Bornier 5V
LED bleu
LED verte
LED rouge
LED orange



Board: 2 copper layers, 72.1 x 85.1 mm, 34 parts (2 on the bottom side), 36 nets.

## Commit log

2013-09-22 Premier commit : Ajout des ressources
    Ce premier commit consiste a rassembler tous les documents concernant ce
    projet.
    [ACAD_FREEWAY_COMPONENT_2-2.sldprt, ACAD_FREEWAY_COMPONENT_3-2.sldprt, Base_PMT1.SLDASM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]
2013-09-22 Avancement de la carte de base
    [PRoMo_Base_CMS.sch]
2013-10-01 Choix des pins et début du routage
    [Liste des Pins.xlsx, PRoMo_Base_CMS.brd, PRoMo_Base_CMS.sch]
2014-06-18 Utilisation Lib SeeedStudio
    [Ballcaster.SLDPRT, Ballcaster_2.SLDPRT, Ballcaster_3.SLDPRT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]
2014-06-21 Schématique OK, début routage
    [PRoMo_Base_CMS.brd, PRoMo_Base_CMS.sch]
2015-06-01 Routage done, mais revoir schématique
    [Liste des Pins.xlsx, PRoMo_Base_CMS.brd, PRoMo_Base_CMS.sch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]
2016-11-15 Clean Up and Add start for 3D
    [ACAD_FREEWAY_COMPONENT_2-2.sldprt, ACAD_FREEWAY_COMPONENT_3-2.sldprt, Ball.sldasm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]
2016-11-15 Finish cleaning and add create base for Eagle files
    [Ball.sldasm, Ball.sldprt, Bottom.SLDASM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]
2018-10-27 Switch for PIC to ARM, basic project start
    Based on STM32F411RE Nucleo board, basic functions and basic encoder
    code working
2018-10-28 Add motor basic support, switch to proto shield
2018-10-31 Improve Makefile and basic UART rx
2020-10-27 Move to Kicad and schematic Design almost done
    [Communication.sch, Liste des Pins.xlsx, Motor_driver.sch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]
2020-11-01 Schematic update and placement DONE
    [Communication.sch, Motor_driver.sch, Motor_outline.dxf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]
2020-11-07 Routing Done, All files ready for ordering
    [Communication.sch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]
2020-11-20 Prepare Electronics v0.2, Add ballcaster holder file
    [BallCaster Support.stl, Communication.sch, Motor_driver.sch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]
2021-02-14 Small update to schematic and todo
    [Motor_driver.sch, PRoMo.sch]
2021-09-11 Start working on HW v0.2
    [Communication.sch, Motor_driver.sch, PRoMo.kicad_pcb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]
